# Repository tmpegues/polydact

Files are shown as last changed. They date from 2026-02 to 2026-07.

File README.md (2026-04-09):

# Polydact: a flexible extra digit
[Polydact on portfolio](tmpegues.github.io/project/polydact)
## Overview
Polydact is a wearable robotic sixth finger that gives its user greater dexterity than they have with their natural hand. The device is controlled by a glove with embedded flex sensors, as shown in the video below.

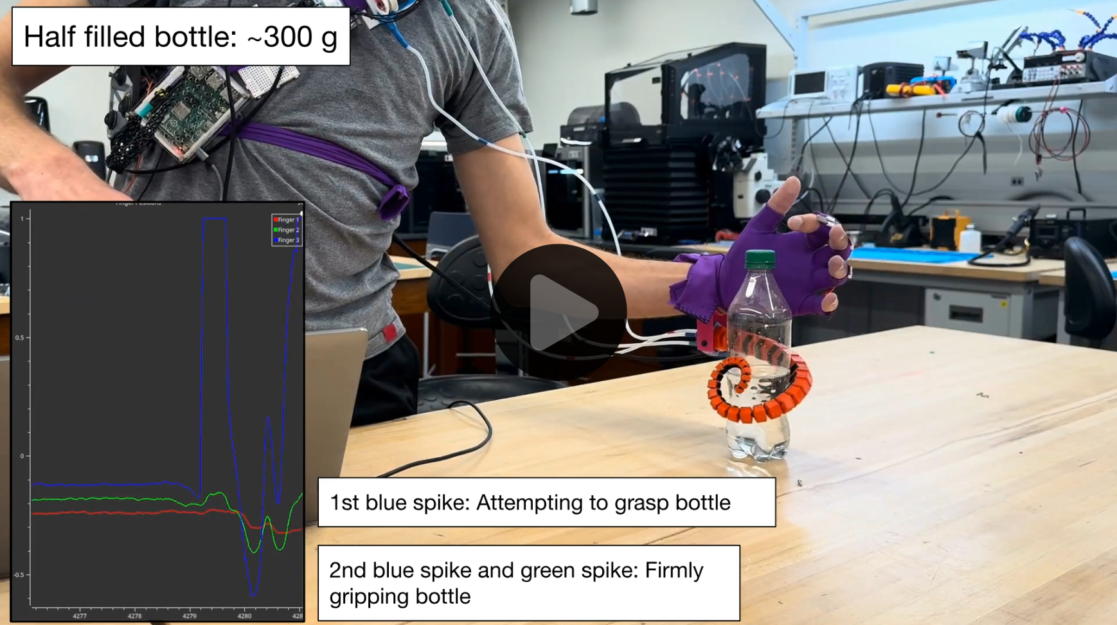
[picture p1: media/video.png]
Polydact in use (https://youtu.be/Mq05AG6Wxf4)

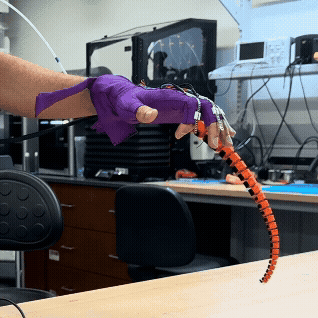
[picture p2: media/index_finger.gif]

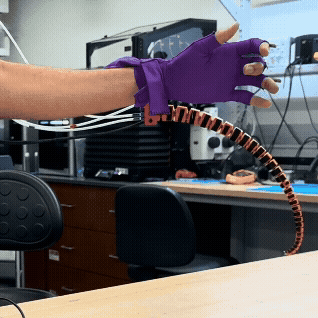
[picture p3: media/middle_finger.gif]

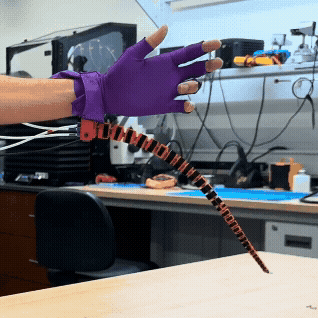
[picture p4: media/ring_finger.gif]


## Hardware Required
There are four main parts of the device: the tentacle itself, a control device, actuators, and electronics. *Italicized* parts are off the shelf parts that can be purchased. **Bolded** parts are custom designed and must be fabricated.

### 1. Tentacle
Four parts are required:
1. [**Tentacle**](/design/3d_files/multi_material_tentacle/)
    * Import all STL files to slicer as a single object with multiple parts
2. [**Socket**](/design/3d_files/hand_bracket/adjustable_mount_socket.stl)
3. [**Wrist mount**](/design/3d_files/hand_bracket/adjustable_mount_hand_bracket.stl)
4. A strap is also required to attach the wrist mount to the user.

### 2. Control Device
A glove with three flex sensors attached is the recommended control device. Below is an image and circuit diagram of the glove created for this project. It uses 3 *[Spectra Symbol flex sensors](https://www.adafruit.com/product/1070)*.

Control glove and circuit diagram

### 3. Actuation
Six parts are required:
1. *Motors*
    * *Robotis Dynamixel XM430-W210-T* were used for this project.
2. [**3x Motor Frames**](/design/3d_files/motor_parts/motor_frame.stl)
3. [**Motor Strap**](/design/3d_files/motor_parts/motor_strap/)
    * Import all STL files to slicer as a single object with multiple parts
4. [**3x Spools**](/design/3d_files/motor_parts/spool.stl)
    * [**Spool Tops**](/design/3d_files/motor_parts/spool_top.stl) are optional, but help retain tendons on spools
5. *A flexiblie, inextensible wire or thread to be used as a cable or tendon.* Braided fishing line is used for this project.
6. *Guide tubes* for routing the tendon from the motors to the tentacle.

### 4. Electronics
Two functions are required: the ability to interface with the control device and to interface with the motors. Two options are suggested:
1. Use a *Raspberry Pi* with external analog to digital converter (ADC). An eight-channel *MCP3008 ADC* is used for this project, but only three channels are required.
    * The Raspberry Pi will interface with the control device using the ADC and control the motors by connecting to the U2D2 using USB.
2. Use a laptop or other full featured computer connected by USB serial to a microcontroller with built-in ADC that interfaces with the control device.
    * [Example code](/pico_serial_sensor/) is provided to use a *Raspberry Pi Pico 2* to inferface with the control device.

Power: A 12 V battery can be used connected to the U2D2 Power Hub directly, and the Raspberry Pi through a buck converter to allow use of the device not tethered to an external power supply.

## Assembly
Using a battery powered Raspberry Pi for motor control with ADC for control device interface:
1. Thread tendons through the holes in the tentacle, socket, and guide tubes. Tie all three tendons in a knot at the free end of the tentacle.
    * It can be helpful to place two sections of heat-shrink tubing over on each guide tube to fix them to the socket and motor frames.
2. Place two M3 screw through holes on opposite faces of the socket and wrist mount. Adjust the angle of the socket relative to the wrist mount and tighten using nuts on the outside of the wrist mount.
3. If the tentacle is loose in the socket, hex nuts can be placed in the counterbores on the inside of the socket and screws can then be used to hold the tentacle in place.
4. Individually tie or otherwise fix the free ends of the the tendons to their own spools.
5. Screw spools onto motors and attach frames
    * If using heat shrink on guide tubes, this is a good time to shrink the tubes onto both the socket and motor frames
6. Attach switch box, Raspberry Pi, U2D2 and Power Hub, and motor strap to chest strap and tie diagonally across the user's chest.
7. Attach wrist mount to strap and tie strap to user's wrist.
8. Slide motors into motor strap.
9. Admire your handiwork

## ROS Setup
Packages `polydact` and `polydact_interfaces` are written for ROS 2 Kilted and can be downloaded and built with
```
git clone https://github.com/tmpegues/polydact.git
cd polydact
rosdep install --from-paths src --ignore-src
colcon build --paths src/*
source install/setup.bash
```
After installing dependencies, building workspace, and sourcing, you will be ready to launch.

## Launching
The main launchfile can be used with
```
ros2 launch polydact polydact.launch.xml sensor_source:=pi motors:=true control_mode:=0 plotter:=false
```
This will launch both the `pi_adc_sensor_node` and `motor_coordinator` nodes.
* `sensor_source` can be changed to `serial` to use a serial device over USB instead.
* `motors:=true` launches the `motor_coordinator` node.
    * If developing or troubleshooting a control device, `motors:=false` will not launch the `motor_coordinator_node`, allowing for focus on teh sensor node.
* `control_mode:=0` will initialize the motors with torque off.
    * After sensor calibration, motor torque can be activated with `ros2 service call /set_mode polydact_interfaces/srv/Mode '{mode: 1}'`
* `plotter:=false` will not open the PlotJuggler visualization of sensor positions.
    * When controlling the device from a Raspberry Pi, it is recommended to run PlotJuggler on another device that can receive the ROS topics so the Polydact user can see that their finger movements are being read properly.

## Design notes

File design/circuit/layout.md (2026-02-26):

Parts

| Part ID | Part | Location | Communication with | Power to | Power from |
| --- | --- | --- | --- | --- | --- |
| 01 | Battery | Belt | | 02, 03 | |
| 02 | Converter | Bandoleer | | 05 | 01 |
| 03 | U2D2 | Bandoleer | 04, 05 | | 01 |
| 04 | Motors | Shoulder strap | 03 | | |
| 05 | R Pi | Bandoleer | 03, 06, 08, 09, 10, 11 | 06, 08 | |
| 06 | ADC in (bread)board  | Bandoleer | 05, 07 | 07 | 05 |
| 07 | Flex Sensors | Glove | 06 | | 06 |
| 08 | Slide Pot | Bandolier | 05 | | 08 |
| 09 | Button 1 (Unlock) | Glove | 05 | | 05 |
| 10 | Button 2 (Loosen) | Glove | 05 | | 05 |
| 11 | Button 3 (Calibrate) | Bandolier | 05 | | 05 |
Wires

| IDs | Type | Length | Connectors |
| ----- | --- | --- | --- |
| 01_02 | Power | Short | |
| 01_03 | Power | Long | |
| 02_05 | Power | Long | X, USB-C |
| 03_04 | TTL | Short (available) | TTL |
| 05_03 | USB | Short (available) | USB-A, micro USB |
| 05_06 | Comm | Short | pin (3), pin (3) |
| 05_06 | Power | Short | pin (2), pin (4) |
| 05_08 | Comm and Power | Short | pin (4), pin (4) |
| 05_09 | Comm and Power | Long | pin (3), pin (2) |
| 05_10 | Comm and Power | Long | pin (3), pin (2) |
| 05_11 | Comm and Power | Short | pin (2), pin (2) |

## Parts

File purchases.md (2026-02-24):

| Category | Item | PN | Qty | Total Price | Put on sheet? | Received |
| --- | --- | --- | --- | --- | --- | --- |
| Glove | [Batting gloves](https://www.amazon.com/Franklin-Sports-20965F4-Shok-Sorb-Batting/dp/B07GJQBRMX) | | 2 Pair | 34.52 | 0113 | O |
| Glove | [Flex Sensors](https://www.adafruit.com/product/1070#technical-details) | | 10 | 71.60 | 0113 | O |
| Glove | [Stretch Rubber Sensor](https://www.adafruit.com/product/519) | | X | - | Lab Stock | O |
| Tentacle | [KV Flex 90](https://www.reynoldsam.com/product/kxflex) | | 1 | 34.47 | 0129 | O |
| Glove | [Conductive Nylon Tape](https://www.adafruit.com/product/3961) | | 1 | 2.95 | 0205 | O |
| Glove | [Velostat Sheet](https://www.adafruit.com/product/1361) | | 1 | 4.95 | 0205 | O |
| Glove | [Sewing Snaps](https://www.adafruit.com/product/1126) | | 1 | 3.95 | 0205 | O |
| Glove | [Steel Thread](https://www.adafruit.com/product/640) | | 1 | 6.95 | 0205 | O |
| Glove | [Lycra](https://www.amazon.com/Spandex-Fabric-Swimwear-Activewear-Stretch/dp/B0CJHF49Y2) | | 2 yd | 31.80 | 0205 | O |
| Glove | [Stretch iron-on tape](https://www.amazon.com/HeatnBond-SoftStretch-Ultra-Iron-Adhesive/dp/B01N1T2IYZ) | | 1 | 4.43 | 0205 | O |
| Glove | [Neoprene](https://www.amazon.com/FLKQC-Neoprene-Adhesive-Multiple-Dimensions/dp/B09TXFBNWH) | | 1 | 10.99 | 0205 | O |
| Mechanical  | [PTFE Tubing 4 OD, 2 ID](https://www.mcmaster.com/52335K32/) | | 10 ft  | 31.20 | x | O |
| Mechanical  | [PE Tubing, 4 OD](https://www.mcmaster.com/51555K121/) | | 25 ft  | 8.25 | 0220 | O |
| Electronics | [Rasberry Pi 4, 4 GB](https://www.adafruit.com/product/4296) | Ada 4296 | 1 | 75.00 | 0224 | X |
| Electronics | [MCP3008 ADC](https://www.adafruit.com/product/856) | 856 | 1 | 4.50 | 0224 | X |
| Electronics | [UEBC Buck Converter](https://www.adafruit.com/product/1385) | | 1 | 9.95 | 0224 | X |
| Electronics | [NeoSlider](https://www.adafruit.com/product/5295) | | 1 | x | Lab Stock | O |
| x | x | | x | x | x | x |
| x | x | | x | x | x | x |

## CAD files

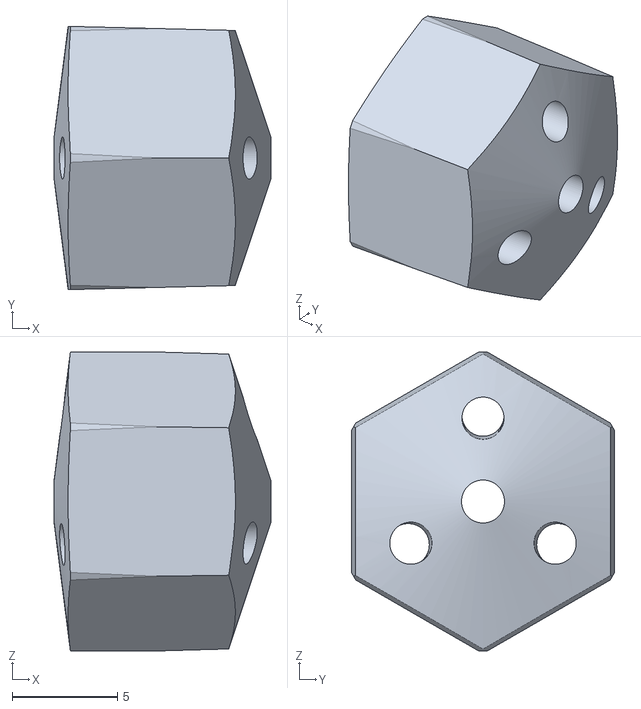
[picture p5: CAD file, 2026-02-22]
design/3d_files/multi_material_tentacle/3D for full printing - Part 13.stl
10.3 x 12.5 x 14.2

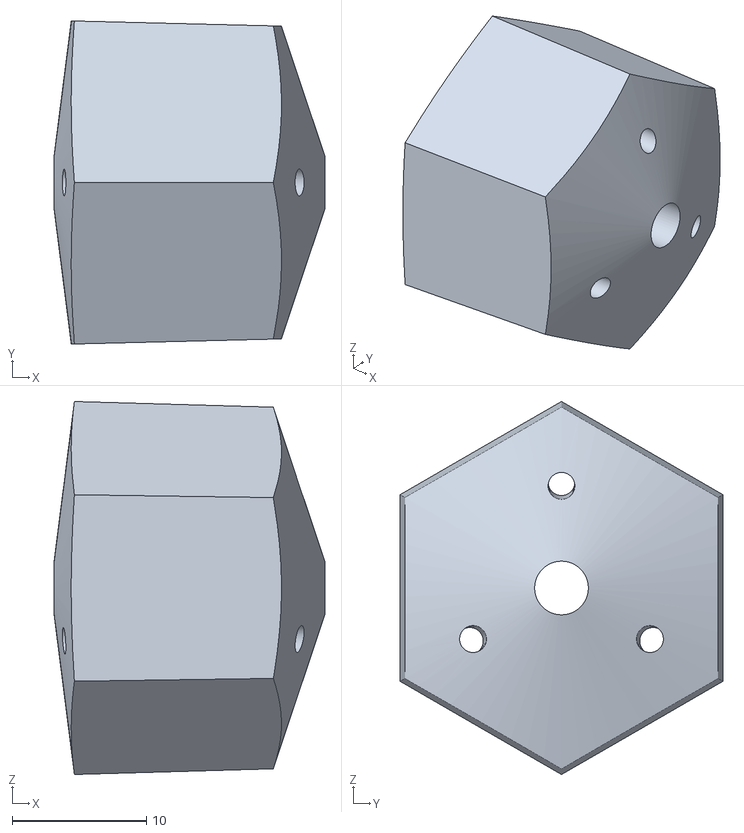
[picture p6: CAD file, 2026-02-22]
design/3d_files/multi_material_tentacle/3D for full printing - Part 28.stl
20.2 x 24.1 x 27.8

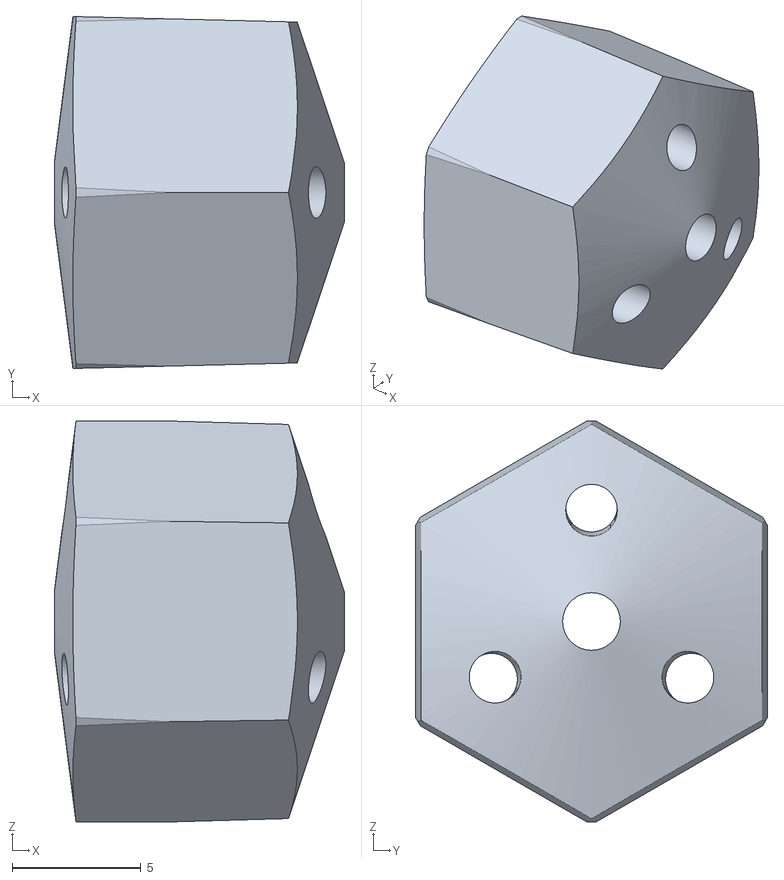
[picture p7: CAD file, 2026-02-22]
design/3d_files/multi_material_tentacle/3D for full printing - Part 15.stl
11.3 x 13.6 x 15.5

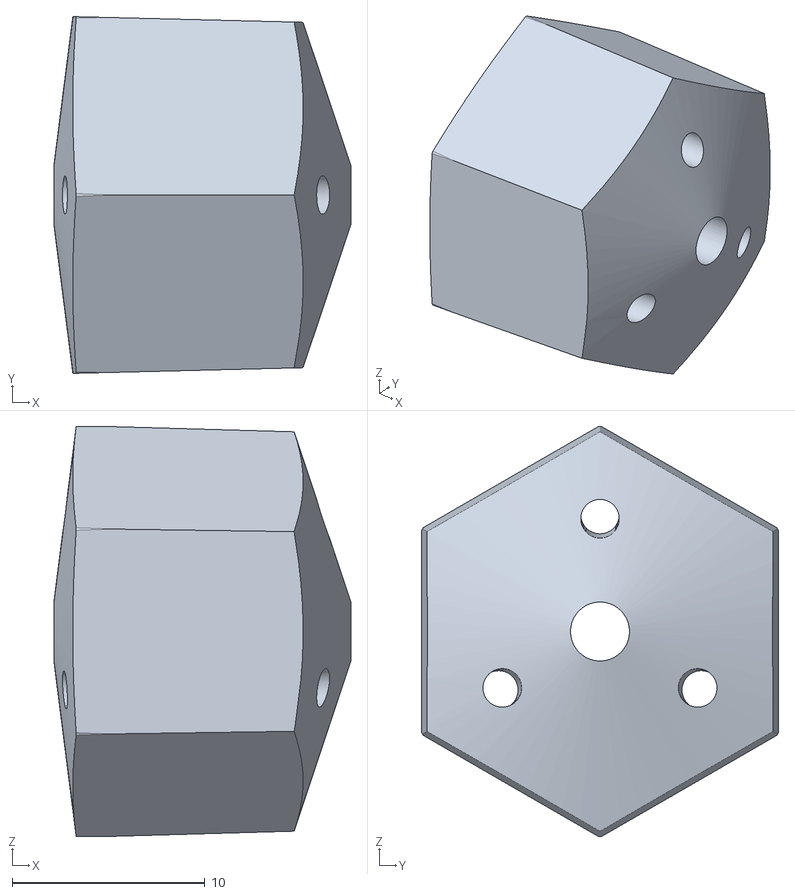
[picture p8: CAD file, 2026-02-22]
design/3d_files/multi_material_tentacle/3D for full printing - Part 22.stl
15.4 x 18.5 x 21.3

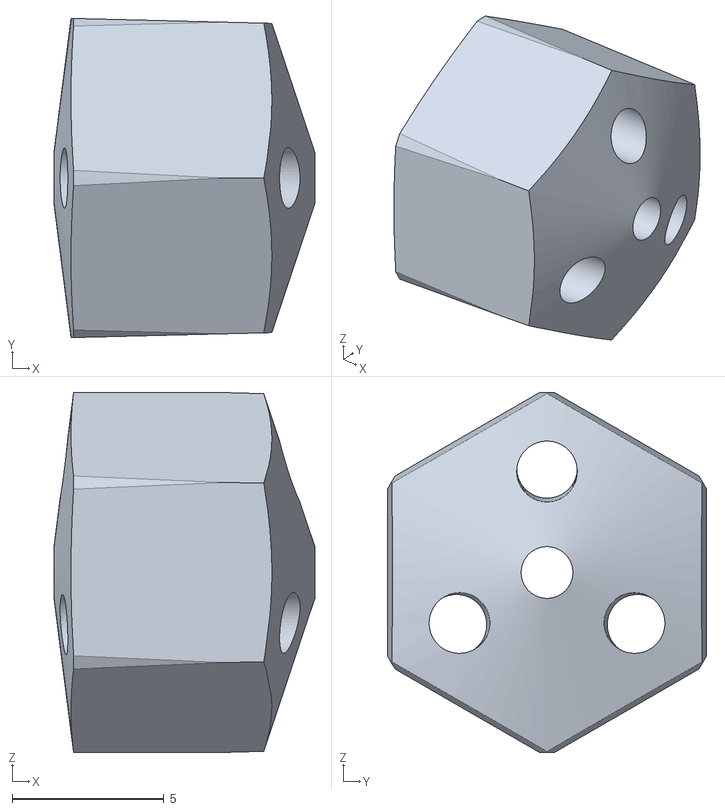
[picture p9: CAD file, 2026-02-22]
design/3d_files/multi_material_tentacle/3D for full printing - Part 9.stl
8.60 x 10.5 x 11.9

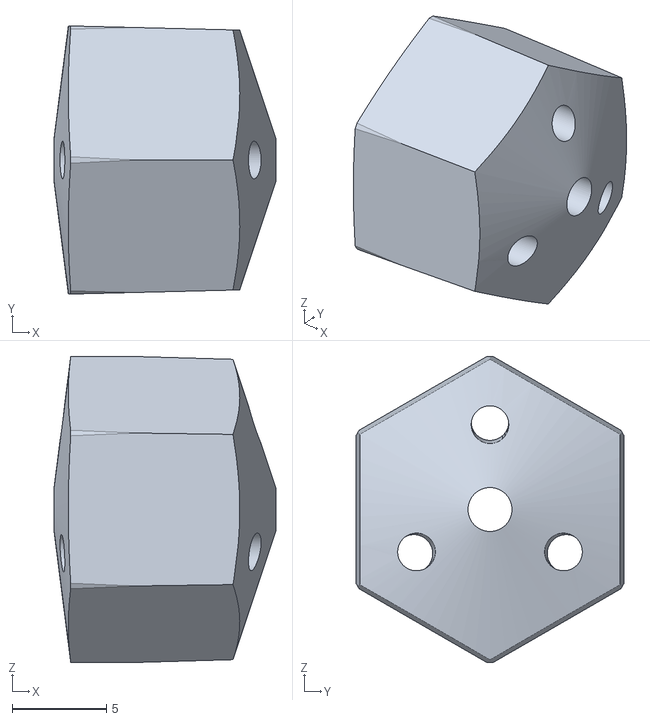
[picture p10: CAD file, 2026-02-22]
design/3d_files/multi_material_tentacle/3D for full printing - Part 16.stl
11.8 x 14.3 x 16.3

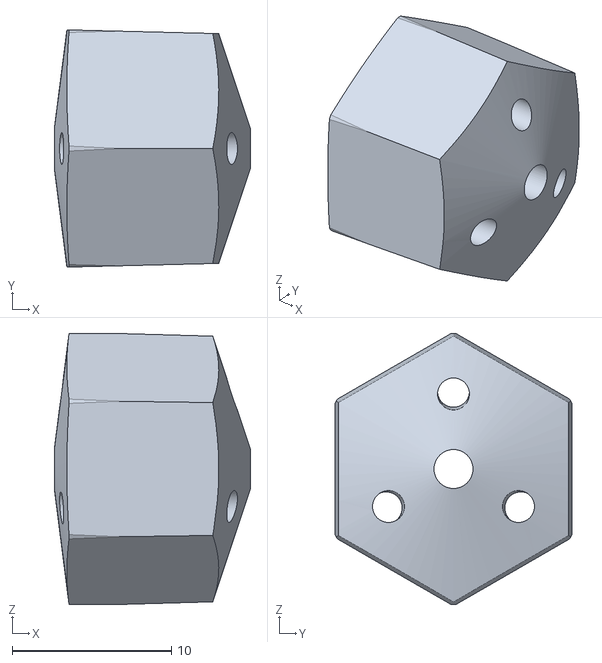
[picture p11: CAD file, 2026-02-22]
design/3d_files/multi_material_tentacle/3D for full printing - Part 17.stl
12.3 x 14.9 x 17.0

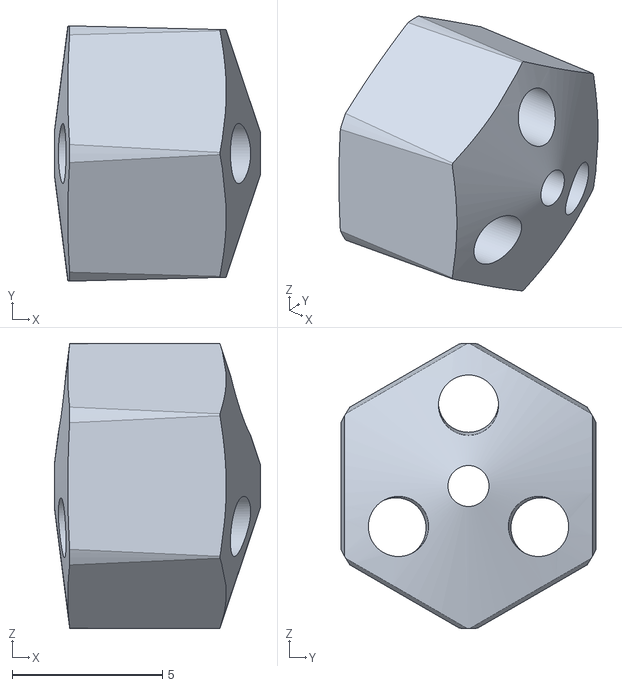
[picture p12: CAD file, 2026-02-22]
design/3d_files/multi_material_tentacle/3D for full printing - Part 4.stl
6.87 x 8.50 x 9.49

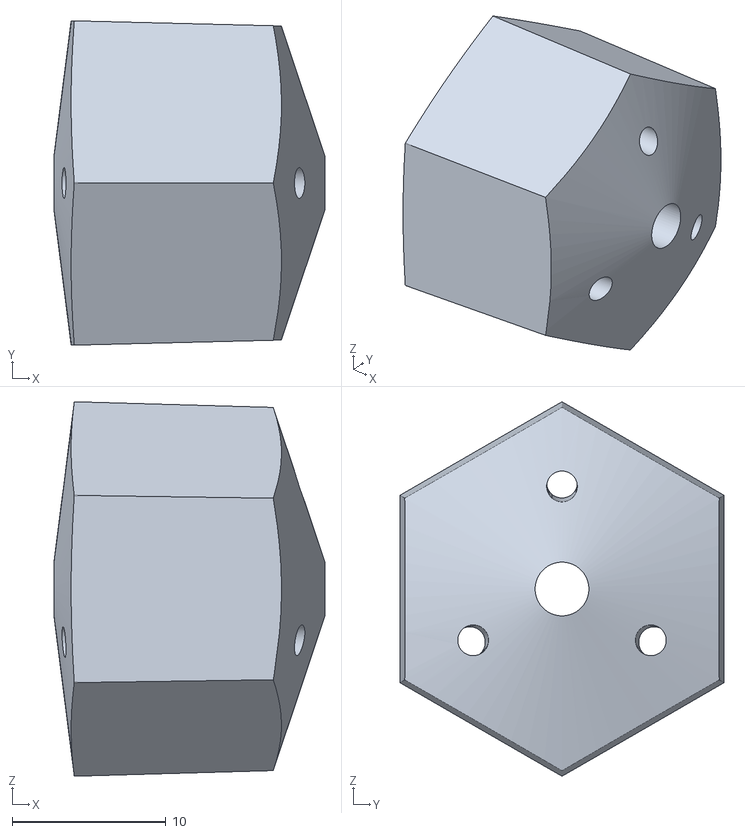
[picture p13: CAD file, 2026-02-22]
design/3d_files/multi_material_tentacle/3D for full printing - Part 25.stl
17.6 x 21.1 x 24.4

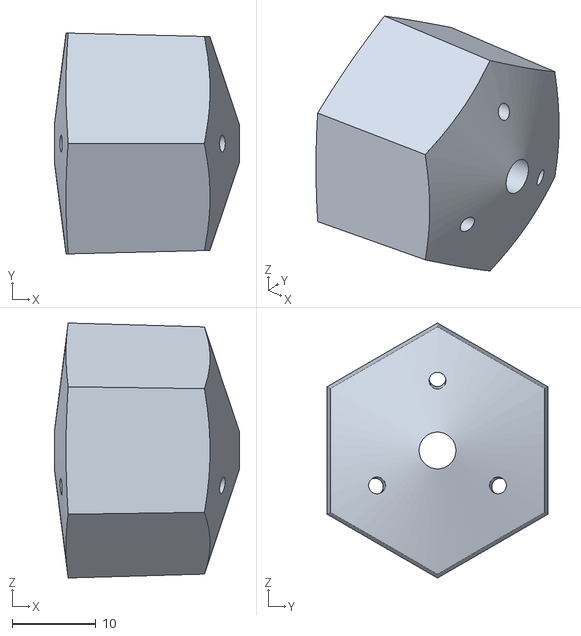
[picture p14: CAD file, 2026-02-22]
design/3d_files/multi_material_tentacle/3D for full printing - Part 30.stl
22.1 x 26.3 x 30.4

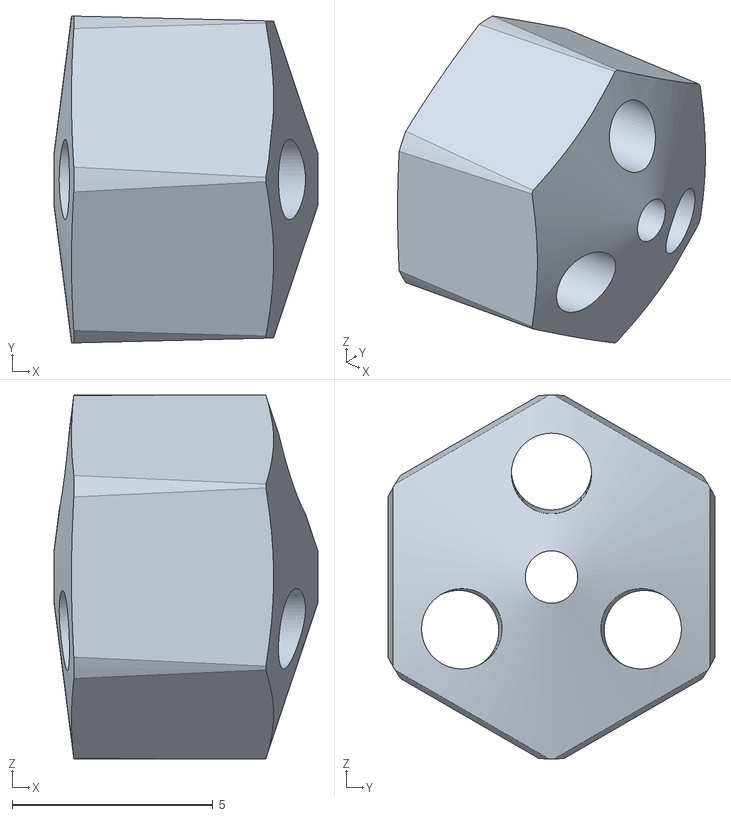
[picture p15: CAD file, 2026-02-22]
design/3d_files/multi_material_tentacle/3D for full printing - Part 3.stl
6.57 x 8.15 x 9.07

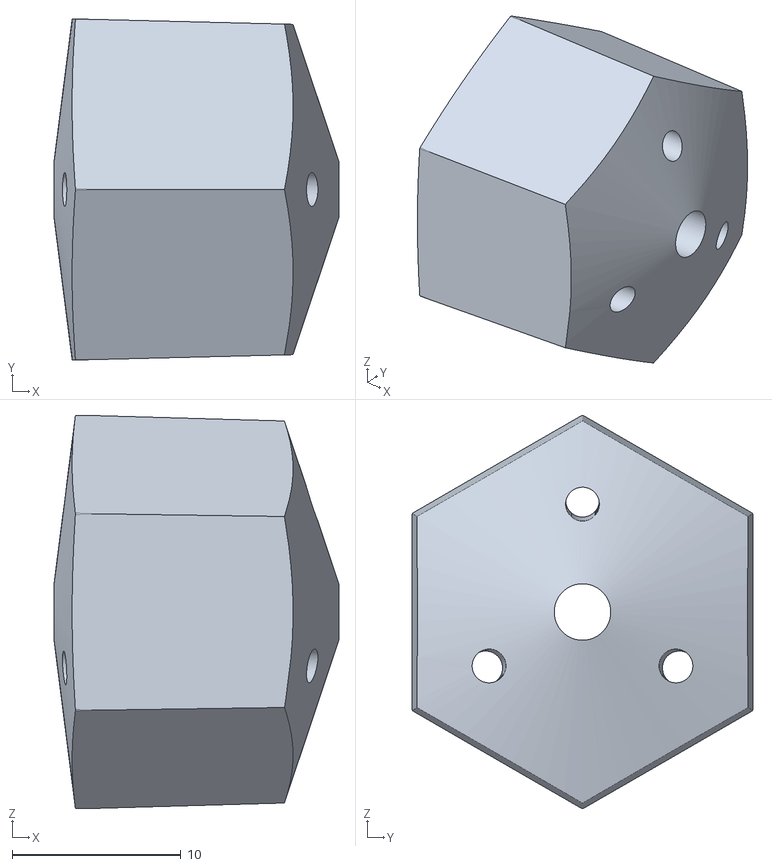
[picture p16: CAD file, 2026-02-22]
design/3d_files/multi_material_tentacle/3D for full printing - Part 24.stl
16.9 x 20.2 x 23.3

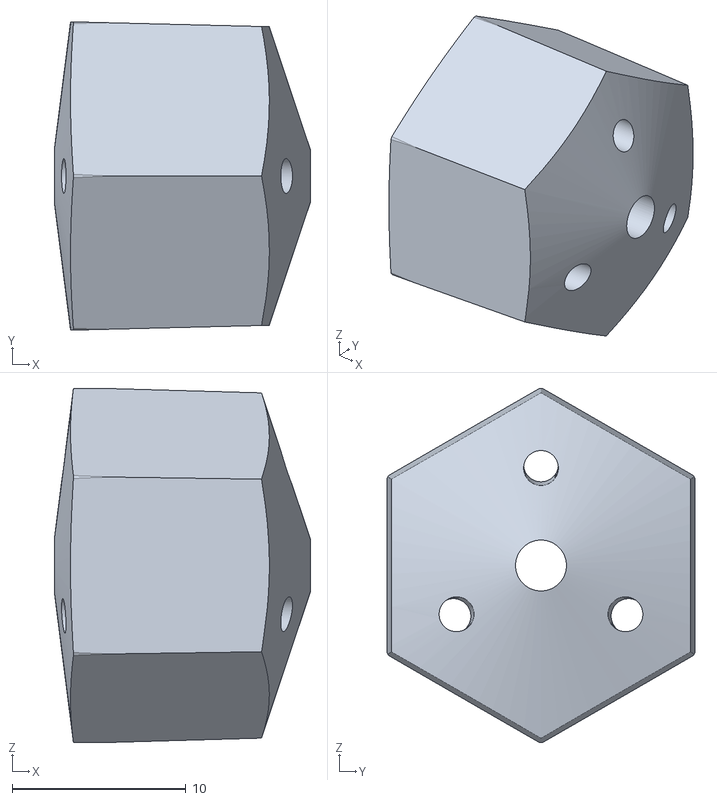
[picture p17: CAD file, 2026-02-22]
design/3d_files/multi_material_tentacle/3D for full printing - Part 21.stl
14.7 x 17.7 x 20.4

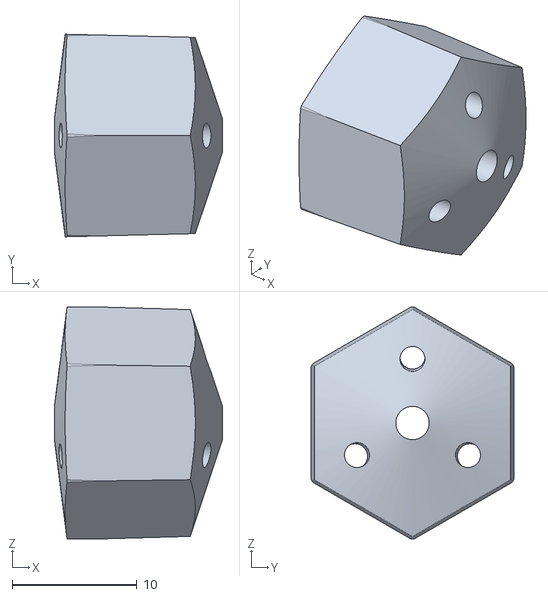
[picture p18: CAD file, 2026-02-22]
design/3d_files/multi_material_tentacle/3D for full printing - Part 19.stl
13.5 x 16.2 x 18.6

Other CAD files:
design/3d_files/multi_material_tentacle/3D for full printing - Part 11.stl
design/3d_files/multi_material_tentacle/3D for full printing - Part 29.stl
design/3d_files/multi_material_tentacle/3D for full printing - Part 12.stl
design/3d_files/multi_material_tentacle/3D for full printing - Part 20.stl
design/3d_files/flex_slider.stl
design/3d_files/hand_bracket/adjustable_mount_hand_bracket.stl
design/3d_files/hand_bracket/adjustable_mount_socket.stl
design/3d_files/motor_parts/motor_base.stl
design/3d_files/motor_parts/motor_frame.stl
design/3d_files/motor_parts/motor_strap/strap_band.stl
design/3d_files/motor_parts/motor_strap/strap_slide_base_single (1).stl
design/3d_files/motor_parts/motor_strap/strap_slide_base_single (2).stl
design/3d_files/motor_parts/motor_strap/strap_slide_base_single.stl
design/3d_files/motor_parts/spool.stl
design/3d_files/motor_parts/spool_top.stl
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

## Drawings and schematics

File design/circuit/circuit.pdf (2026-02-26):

05

06

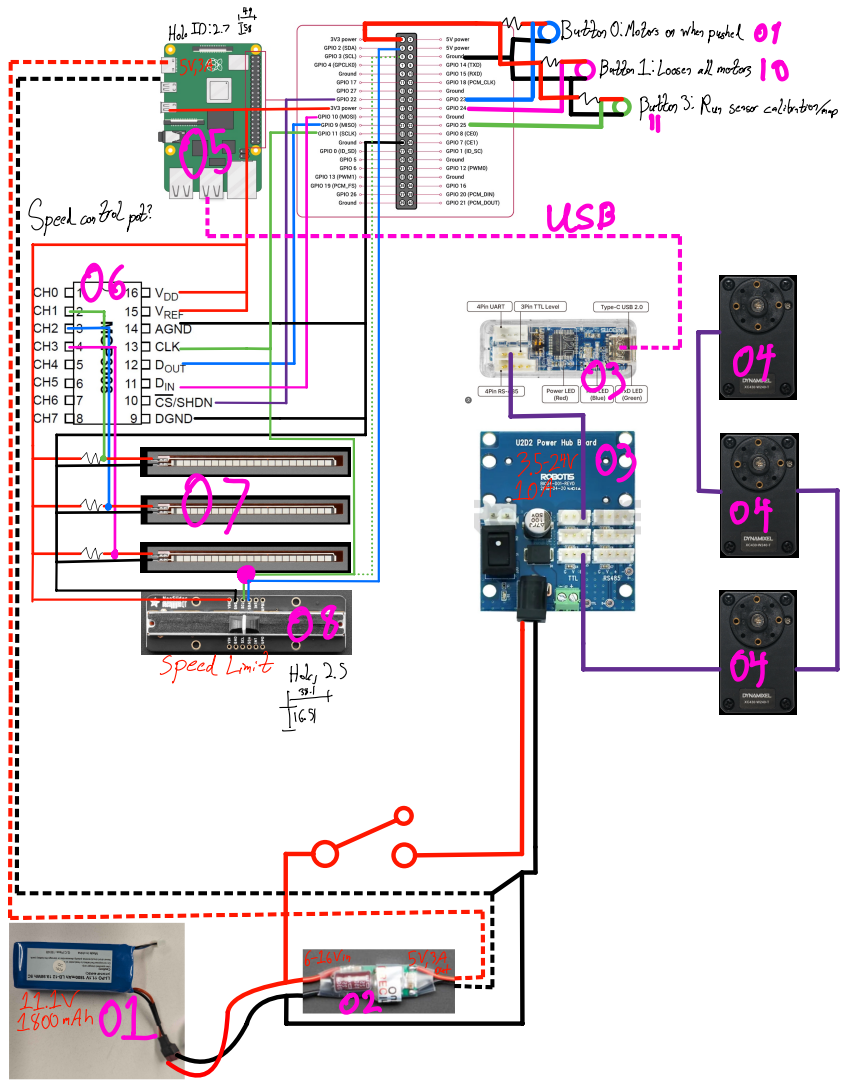
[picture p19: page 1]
Hol.IO27 I; ButtonOMotorsonwhenpushed09; Button1Loose allmotors 0; Python Runsensorcalibrationmap; Speedcontrolpot; USB; 08 04 speedlinitI.fi; 6 16Vin5V 3Aut-1EtAnO1 ⁰²

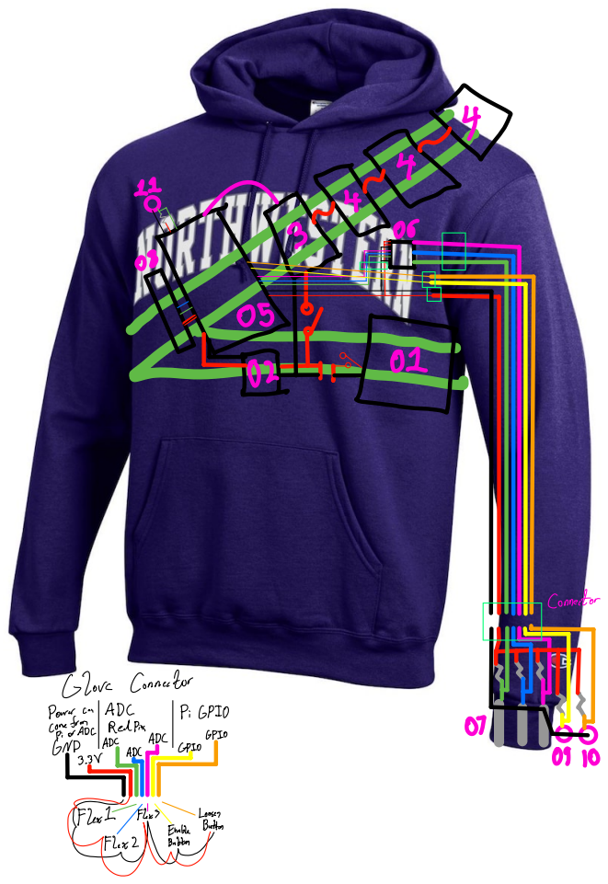
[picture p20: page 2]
Connector; 222 Glove Connector; t.itiianii; Ellenville

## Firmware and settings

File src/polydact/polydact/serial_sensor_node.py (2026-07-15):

"""Read the serial monitor from the Pico 2 to publish a motor goal."""

from polydact_interfaces.msg import MotorGoal
import rclpy
from rclpy.node import Node
from rclpy.qos import QoSDurabilityPolicy, QoSProfile
from std_srvs.srv import Empty
from polydact.sensor import Sensor

import serial


class SerialReader(Node):
    """Reads the serial monitor and publishes motor goals."""

    def __init__(self):
        """Initialize serial reader and goal publisher."""
        super().__init__('serial_reader')

        # Creating publisher first to that PlotJuggler doesn't have to wait for calibration
        self.goal_pub = self.create_publisher(
            MotorGoal,
            'motor_goal',
            QoSProfile(depth=10, durability=QoSDurabilityPolicy.TRANSIENT_LOCAL),
        )

        self.remap_srv = self.create_service(Empty, 'remap', self.remap_cb)

        # Get motor list and initialize sensors
        self.declare_parameter('sensor_ids', [1, 2, 3])
        sensor_ids = self.get_parameter('sensor_ids').value

        self.declare_parameter('motor_ids', [1, 2, 3])
        self.motor_ids = self.get_parameter('motor_ids').value

        self.declare_parameter('calibration_len', 400)
        self.calibration_len = self.get_parameter('calibration_len').value

        self.sensors = {}
        for sensor_id, motor_id in zip(sensor_ids, self.motor_ids):
            self.sensors.update({sensor_id: Sensor(sensor_id, motor_id)})

        # Set up serial port
        self.declare_parameter('serial_port', '/dev/ttyACM0')
        port = self.get_parameter('serial_port').value
        self.get_logger().info(f'serial port: {port}')

        self.s_port = False
        while not self.s_port:
            try:
                self.s_port = serial.Serial(port, 115200, timeout=10)
            except serial.SerialException:
                self.get_logger().error('Serial device not found.', throttle_duration_sec=1)

        # Calibrate sensor min/max with specified number of readings from each sensor
        self.min_max_calibration(self.calibration_len)

        # Begin publishing normalized sensor readings
        self.pub_freq = 100
        read_freq = 300
        self.last_published = 0
        # Make sure I'm reading slightly faster than serial is printing
        read_freq *= len(self.sensors) + 0.1

        self.reading_timer = self.create_timer(1 / read_freq, self.reading_timer_callback)
        self.publishing_timer = self.create_timer(
            1 / self.pub_freq, self.publishing_timer_callback
        )
        self.get_logger().info('Serial Reader fully initialized')

    def full_calibration(self, num_points: int):
        """
        Calibrate the glove by finding min and max flexes for all fingers, then remap to motors.

        Args:
        ----
        num_points (int): How many points are to be collected for the min max calibration?

        """
        self.freeze(True)

        self.min_max_calibration(num_points)
        self.map_sensor_to_motor()

        self.freeze(False)

    def freeze(self, freeze_on: bool, read: bool = False):
        """
        Stop all motors by pausing timer, then sending Goal = 0.

        Saving of sensor values can also be paused optionally, but unfreezing will always restart
        sensor saving.

        Args:
        ----
        freeze_on (bool): True will stop motors, False will turn velocity control back on
        read (bool): True will also top lines from being saved, which is used for remapping.

        """
        match freeze_on:
            case True:
                if read:
                    self.reading_timer.cancel()
                self.publishing_timer.cancel()
                for motor_id in self.motor_ids:
                    self.goal_pub.publish(MotorGoal(motor_id=motor_id, goal=0))

            case False:
                for sensor in self.sensors.values():
                    sensor.fill_average()
                self.publishing_timer.reset()
                self.reading_timer.reset()

    def get_max_diff(self, reads: int = 100) -> int:
        """
        Get the ID of the sensor that gets bent the most over the next selected no of serial lines.

        Args:
        ----
        reads (int): How many serial lines to read. Not how many per sensor.

        Returns
        -------
         (int): The ID of the sensor that experienced the largest bend. -1 means there was an issue

        """
        # Clear the saved selector values
        for sensor in self.sensors.values():
            sensor.selector_min = 10000
            sensor.selector_max = -10000

        i = 0
        # Read the selected total number of lines
        while i <= reads:
            line = self.get_line()
            if line:
                id, read = line
                if id not in self.sensors:
                    self.get_logger().error(f'Sensor message id {id} is not valid id.')
                    break
                sensor = self.sensors[id]
                if read > sensor.selector_max:
                    sensor.selector_max = read
                elif read < sensor.selector_min:
                    sensor.selector_min = read
                else:
                    self.get_logger().error(
                        f'Unexpected condition in sensor remapping. Serial line: {line}'
                    )

        # Now that lines are read, determine which sensor has been flexed the most
        diff = 0
        max_bent = -1
        for id, sensor in self.sensors.items():
            if abs(sensor.selector_max - sensor.selector_min) > diff:
                diff = sensor.selector_max - sensor.selector_min
                max_bent = id

        return max_bent

    def remap_cb(self, request, response):
        """
        Remap sensors.

        Args:
        ----
        request (std_srv/srv/Empty): unused
        response (std_srv/srv/Empty): unused

        """
        self.map_sensor_to_motor()

    def map_sensor_to_motor(self):
        """Change the assignment of which sensor controls which motor."""
        self.freeze(True, True)
        retry = True
        while retry:
            retry = False
            # Clear motor ids for all sensors
            for sensor in self.sensors.values():
                sensor.motor_id = -1

            # Cycle through motors again, setting sensors as we go
            for motor in self.motor_ids:
                self.get_logger().info(f'Motor: {motor}')
                while True:
                    self.get_logger().info(f'Wiggle the sensor to use with motor {motor}')
                    # Read for 100 values, find max bent sensor
                    sensor1 = self.get_max_diff(100)
                    self.get_logger().info(f'Sensor {sensor1} selected for {motor}')
                    self.get_logger().info(f'Keep wiggling sensor {sensor1} to confirm selection')
                    # Read another 100, check for match
                    sensor2 = self.get_max_diff(100)
                    # If the sensors match and that sensor doesn't have a motor saved yet, save
                    if sensor1 == sensor2 and self.sensors[sensor1].motor_id == -1:
                        self.sensors[sensor1].motor_id = motor
                        self.get_logger().info(f'Saving: Sensor {sensor1} maps to motor {motor}')
                        break
                    elif sensor1 != sensor2:
                        self.get_logger().error(
                            f'1st sensor {sensor1} and 2nd sensor {sensor2} do not match.'
                        )
                    elif self.sensors[sensor1].motor_id != -1:
                        self.get_logger().error(
                            f'Sensor {sensor1} already assigned: {self.sensors[sensor1].motor_id}.'
                        )
                    self.get_logger().info(f'Retrying. Motor = {motor}.')

            # Check that each sensor has a motor (id != -1) and that each motor is unique
            motor_list = self.motor_ids.copy()
            for s_id, sensor in self.sensors.items():
                if sensor.motor_id in motor_list:  # This case is what we want
                    self.get_logger().info(f'Sensor {s_id} is assigned to motor {sensor.motor_id}')
                    motor_list.remove(sensor.motor_id)
                elif sensor.motor_id == -1:
                    retry = True
                    self.get_logger().error(f'Sensor {s_id} was not assigned a motor')
                    break
                elif sensor.motor_id not in motor_list:
                    retry = True
                    self.get_logger().error('This motor is already  assigned or is invalid ID.')
                    break
                else:
                    self.get_logger().error(f'Unexpected case. S: {s_id}, M: {sensor.motor_id}')

            # Check that each motor was assigned
            if len(motor_list) != 0:
                retry = True
                self.get_logger().error(f'Motors unassigned: {motor_list}.')

            if retry:
                self.get_logger().info('Retrying remapping.')
            else:
                self.get_logger().info('Remapping complete:')
                for sensor in self.sensors.values():
                    self.get_logger().info(f'Sensor {sensor.sensor_id} -> Motor {sensor.motor_id}')
                self.freeze(False)

    def min_max_calibration(self, num_points: int):
        """
        Read values from the connected sensors for a few seconds to determine ranges.

        Args:
        ----
        num_points (int): How many points will be checked to figure out each sensor's min/max range

        """
        calibrated = 0
        loop = 0
        self.get_logger().info(f'Beginning min/max calibration for {len(self.sensors)} sensors.')
        while calibrated < len(self.sensors) * num_points:
            self.get_logger().info(
                f'Loop {loop} ({calibrated}/{len(self.sensors) * num_points})',
                throttle_duration_sec=1,
            )
            loop += 1
            line = self.get_line()
            if line:
                id, read = line
                if id not in self.sensors:
                    self.get_logger().error(f'Sensor message id {id} is not valid id.')
                    break
                sensor = self.sensors[id]
                if sensor.calibrated >= num_points:
                    # If we've already read many points, do not process any further points
                    pass
                elif sensor.calibrated < num_points:
                    # If we haven't read this many points, check against min and max
                    sensor.calibrated += 1
                    calibrated += 1
                    if read > sensor.max:
                        sensor.max = read
                    elif read < sensor.min:
                        sensor.min = read
                    if sensor.calibrated >= num_points:
                        self.get_logger().info(
                            f'Sensor {sensor.sensor_id} has all {num_points} min/max points read.'
                        )
                        sensor.fill_average()
                else:
                    self.get_logger().error(
                        f'Unexpected condition in calibration. Serial line: {line}'
                    )
        self.get_logger().info('Sensor min/max calibration complete:')
        for id, sensor in self.sensors.items():
            self.get_logger().info(f'Sensor {sensor.sensor_id}: {sensor.min} - {sensor.max}')

    def get_line(self):
        """
        Get the most recent serial line.

        Returns
        -------
        (Bool or (int, float)): False if no or invalid serial read, (id, read) if the was valid

        """
        result = False
        line = False
        try:
            line = self.s_port.readline().decode('utf-8').strip()
        except serial.SerialException:
            self.get_logger().error('No device.')
        if line:
            id = int(line[0])
            if id in self.sensors:
                try:
                    read = float(line[2:])
                    result = (id, read)
                    self.get_logger().debug(f'Read: {line}')
                except ValueError:
                    self.get_logger().error(f'Faulty serial line: {line}')

            else:
                self.get_logger().error(f'Unexpected serial line: {line}')
        else:
            self.get_logger().debug('No serial line available.')
        return result

    def reading_timer_callback(self):
        """Read the serial monitor."""
        line = self.get_line()
        if line and line[0] in self.sensors.keys():
            self.sensors[line[0]].new_read(line[1])

    def publishing_timer_callback(self):
        """Publish all motor goals individually."""
        self.get_logger().debug('Publishing Timer')

        self.goal_pub.publish(
            MotorGoal(
                motor_id=self.sensors[list(self.sensors.keys())[self.last_published]].motor_id,
                goal=self.sensors[list(self.sensors.keys())[self.last_published]].get_value(),
            )
        )
        self.last_published += 1
        self.last_published %= len(self.sensors)


def main(args=None):
    """Run the serial_reader node."""
    rclpy.init(args=args)
    node = SerialReader()
    rclpy.spin(node)
    rclpy.shutdown()


if __name__ == '__main__':
    main()

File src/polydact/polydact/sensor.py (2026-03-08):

"""Reading Polydact's flex sensors."""


class Sensor:
    """Sensor class holds values for each individual sensor."""

    def __init__(self, sensor_id, motor_id):
        """
        Initialize the sensor.

        Args:
        ----
        sensor_id (int): Which sensor is this? My finger map is 1 = ring, 2 = middle, 3 = index.
        motor_id (int): What is the Dynamixel ID of the motor that this sensor will control?

        """
        self.sensor_id = sensor_id
        self.motor_id = motor_id
        self.min = 10000.0
        self.max = 0.0
        self.selector_min = 0.0
        self.selector_max = 0.0
        self.smoothing = 10
        self.reads = [0.0] * self.smoothing
        self.calibrated = 0

    def new_read(self, value: float):
        """
        Add the newest raw sensor reading to the rolling list.

        Args:
        ----
        value (float): The new reading to add to the rolling list.

        """
        self.reads.append(value)
        self.reads.pop(0)

    def get_value(self) -> float:
        """
        Get the normalized rolling average of sensor readings.

        Returns
        -------
         (float): The normalized rolling average of sensor readings. If sensor is uncalibrated,
                  0.0 will be returned (freezes the motors).

        """
        if not self.calibrated:
            return float(0.0)
        else:
            value = sum(self.reads) / self.smoothing  # Average
            value -= (self.max + self.min) / 2  # Center at 0
            value /= (self.max - self.min) / 2  # Squash the values down to -1 to 1

            # If the max and min are off for some reason, clamp the values
            if value > 1:
                value = 1
            elif value < -1:
                value = -1
            return float(value)

    def fill_average(self):
        """Fill the reads list with a neutral value so motors initialize stopped."""
        self.reads = [(self.max + self.min) / 2] * self.smoothing

    def reset(self):
        """Clear the calibrated values, but keep the motor id assignment."""
        self.min = 10000
        self.max = 0.0
        self.reads = [0.0] * self.smoothing
        self.calibrated = 0

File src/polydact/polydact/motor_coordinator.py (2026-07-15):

"""Test different control modes of one Dynamixel motor."""

from polydact.dynamixel_interface import Motor, DynamixelInterface
from polydact_interfaces.msg import MotorGoal

from polydact_interfaces.srv import Mode
import rclpy
from rclpy.node import Node
from rclpy.qos import QoSDurabilityPolicy, QoSProfile
from sensor_msgs.msg import JointState
from std_msgs.msg import Header


class MotorCoordinator(Node):
    """
    MotorCoordinator is the intermediary between the control device (glove) and the motors.

    Publishers:
        + "motor_states" (sensor_msgs/msg/JointState) - Actual states of the motors

    Subscribers:
        + "motor_goal" (polydact_interfaces/msg/MotorGoal) - A goal to set a particular motor to

    Services:
        + "set_mode" (polydact_interfaces/srv/Mode) - What Control Mode to set the motor to.
            (0 (off), 1 (vel))

    Parameters
    ----------
        + "motor_ids" - The motor ID to to control with this node
        + "control_mode" - The initial Control Mode to use

    """

    def __init__(self):
        """Initialize motor control."""
        super().__init__('motor_coordinator')
        self.active = 0

        self.dyn = DynamixelInterface(self)

        # Set motors to my settings
        self.declare_parameter('motor_ids', [1, 2, 3])
        self.motor_ids = self.get_parameter('motor_ids').value

        self.declare_parameter('Control_Mode', 1)
        self.mode = self.get_parameter('Control_Mode').value

        self.motors = {}
        for motor_id in self.motor_ids:
            self.motors.update({motor_id: Motor(self.dyn, motor_id)})

        # Motors should initialize off, but loop through just to be sure
        # Should probably ad a check to make sure they're actually all off
        for motor in self.motors.values():
            motor.set_off()

        self.goal_sub = self.create_subscription(
            MotorGoal,
            'motor_goal',
            self.set_single_goal,
            QoSProfile(depth=10, durability=QoSDurabilityPolicy.TRANSIENT_LOCAL),
        )
        self.mode_srv = self.create_service(Mode, 'set_mode', self.switch_mode_cb)

        self.motor_states_pub = self.create_publisher(JointState, 'motor_states', 10)

        self.posi_pub = self.create_publisher(MotorGoal, 'cur_position', 10)
        self.velo_pub = self.create_publisher(MotorGoal, 'cur_velocity', 10)
        self.load_pub = self.create_publisher(MotorGoal, 'cur_load', 10)

        # State reads are blocking serial round-trips; at 100 Hz they saturate the
        # bus and starve the command path. 20 Hz is plenty for telemetry.
        self.timer = self.create_timer(1 / 20, self.timer_callback)
        self.get_logger().info(f'motors: {self.motors.keys()}')
        for motor in self.motors.values():
            motor.set_mode(1)

        self.get_logger().info('Motor Coordinator ready')

    def set_single_goal(self, msg: MotorGoal):
        """
        Set the position, velocity, or PWM goal for a single motor.

        Args:
        ----
        msg (polydact_interfaces/msg/MotorGoal): msg.motor_id is the motor to set the goal for
                                                  msg.goal is the goal to set to

        """
        self.get_logger().debug(f'MotorGoal {msg.motor_id} {msg.goal} received.)')
        if msg.motor_id not in self.motors.keys():
            self.get_logger().error(f'Unexpected motor id received: {msg}')
            return

        deadzone = 0.3
        self.motors[msg.motor_id].set_velocity(-1 * msg.goal, deadzone)

    def switch_mode_cb(self, request, response):
        """
        Switch the control mode of this node's motor.

        Args:
        ----
        request  (polydact_interfaces/srv/Mode):
                request.mode contains value to set as the motor's control mode.
        response (polydact_interfaces/srv/Mode):
                reponse.success is True if the control mode is successfully changed

        """
        response.success = True

        # Filter out invalid values
        if request.mode not in [0, 1]:
            self.get_logger().error(
                f'{request.mode} not valid Control Mode. Use 0 (off), 1 (velocity)'
            )
            response.success = False

        for motor in self.motors.values():
            motor.set_mode(request.mode)

        return response

    def timer_callback(self):
        """Read and publish motor position, velocity, and load."""
        motor_states = JointState(header=Header(stamp=self.get_clock().now().to_msg()))

        for motor in self.motors.values():
            motor.get_state()
            # TODO: Add some sort of checking for if the get_state fails
            motor_states.name.append(str(motor.motor_id))
            motor_states.position.append(motor.position)
            motor_states.velocity.append(motor.velocity)
            motor_states.effort.append(motor.effort)

        self.motor_states_pub.publish(motor_states)


def main(args=None):
    """Run the node."""
    rclpy.init(args=args)
    node = MotorCoordinator()
    rclpy.spin(node)
    rclpy.shutdown()


if __name__ == '__main__':
    main()

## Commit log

2026-01-09 Adding reference. Added modified springs.
    [spring_8mm.stl, spring_8mm_no_mid.stl]
2026-01-12 Adding references and changing to tentacle digit
    Next steps:
    [3_cable_SpiRob.STL, pegues_bone_unit_v1.gcode.3mf]
2026-01-12 New flexible tentacle print parts.
    [3D - Part 1.stl, 3D - Part 10.stl, 3D - Part 11.stl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]
2026-01-13 Various printing trials, mostly 3D.
    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
    [2cable_chain.stl, 3D - Part 10.stl, 3D - Part 11.stl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]
2026-01-14 More stls. Created somthing of a plan for control.
    See control_plan.md
    Next steps: Figure out how to control motors and interface with ROS.
    [3D - Part 10.stl, 3D - Part 11.stl, 3D - Part 12.stl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]
2026-01-14 Formalizing more of control plan.
    Setting details on motor specifics and concept of control with glove.
2026-01-14 More parts
    [3D - Part 17.stl, 3D - Part 18.stl, 3D - Part 19.stl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]
2026-01-27 New tentacle, spool, base designs
    [base_v3.stl, base_with_slots.stl, flex_slider.stl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]
2026-01-28 New testing spools
    [spool_v4.stl, spool_v5.stl]
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2026-01-29 Created a node that can use all Dynamixel controls
    single_motor_test has a subscriber that will set the control mode of the
    motor.
    There's also a subscriber on the /set_position topic that will set the
    goal. There's only that one topic, it doesn't matter what the control
    mode is.
    Next steps: Read sensors
2026-01-29 Created messaage and service for setting motors.
    Goal.msg sets the goal of motor "goal.id" to goal.goal. What this goal
    represents (position, velocity, etc) is not set by the message.
    Set_Mode.srv is to be used to set the control mode of the motors. The
    response represents if the mode was succesfully changed
2026-01-29 Transitioning away from dynamixel_sdk packages
    Switched over to polydact_interfaces Goal message and Mode server in
    single_motor_test.
    single_motor_test:
    + Added switch_mode_cb to use new Goal service.
    ++ created several functions to support this change.
    Next steps: Continue transition
2026-01-29 Created goal callback (did not add PWM) Also autoformatted
    Next steps: add PWM
2026-01-29 Removed old dynamixel_sdk_example code
    Next steps: Add a torque detection cutoff. Coordinate three motors.
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2026-01-31 Added new glove parts.
    [flex_slider_v3.stl, flex_slider_v4.stl, hand_bracket_v1.stl]
2026-02-02 Can control a motor with a gloved flex sensor
    Next steps: Write launch file, control 3 motors.
2026-02-02 Created launch file for single motor
    [single_motor.launch.xml]
2026-02-02 three motor setup works with glove
    [motors.launch.xml]
2026-02-02 Added mode 0 to turn off motors in mode service
    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
    [motors.launch.xml]
2026-02-03 Elaborated on motor_id parameter in launchfile.
    Next steps: Creating sensor class in the serial reader node.
    [motors.launch.xml]
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2026-02-03 Too many changes, all untested
    polydact_interfaces/msg/Goal is now MotorState
    motos.launch.xml:
    + Added all Parameters
    motor_coordinator:
    > Moved getting and publishing state code from timer to own functions
    > All motor pos, vel, loads are now published
    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
    [motors.launch.xml]
2026-02-04 Changed the state messages to an array, but this appears to have slowed it way down
    [motors.launch.xml]
2026-02-04 Further array fixing
    [motors.launch.xml]
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2026-02-04 Fixed lag issue by adding separate reader timer.
    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
2026-02-04 Added better error handling
    [motor_coordinator.py]
2026-02-04 Added plotjuggler config arg, fixed MotorState subscriber
    [motors.launch.xml]
2026-02-04 Changed logging, fixed MotorState cb issue
    [motor_coordinator.py]
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2026-02-05 Removed last vestiges of other control modes.
    [motors.launch.xml]
2026-02-06 Added mold stls, updated purchases
    [mold_bottom.stl, mold_top.stl]
2026-02-11 new designs
    [baseV6.stl, frameV6.stl, mold_bottom_v2.stl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]
2026-02-16 Serial logger prints port, shorter calibration
    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
2026-02-16 Works
    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
    [motors.launch.xml]
2026-02-18 New models, new IDs
    [3D for full printing - 3D Tentacle (1).stl, 3D for full printing - 3D Tentacle (10).stl, 3D for full printing - 3D Tentacle (11).stl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]
2026-02-22 Updating typos and design directories
    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
    [2cable_chain.stl, 3D - Part 1.stl, 3D - Part 10.stl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]
2026-02-22 Updating stl files
    [motor frame.stl, motor_frame.stl, spool_body.stl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]
2026-02-22 Removed or commented use of MotorGoalArray
    [motors.launch.xml]
2026-02-22 Adding calibration and mapping to sensor and readr
    Next steps: Finish fixing up the publishing timer in serial_reader.
    [sensor.py]
2026-02-22 Updated hand bracket for fit with PLA bones
    [hand_bracket.stl]
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2026-02-22 New plotjuggler config, old one kept breaking
    [motors.launch.xml]
2026-02-22 Fixed line too long in motor_coordinator.py
    [motor_coordinator.py]
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2026-02-22 New flex slider. Should be easier to sew
    [flex_slider.stl]
2026-02-24 Changed plotjuggler config, made plogjuggler exit
    [motors.launch.xml]
2026-02-24 Attempting to read motor pos, vel, eff
    Next steps: Need to fix how I'm reading efforts
    [dynamixel_interface.py, motor_coordinator.py]
2026-02-24 Changing stl folder name, creating circuit folder
    [3D for full printing - Part 10.stl, 3D for full printing - Part 11.stl, 3D for full printing - Part 12.stl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]
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2026-03-08 new STLs, adding MotorGoal
    [3D for full printing - Part 10.stl, 3D for full printing - Part 11.stl, 3D for full printing - Part 12.stl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]
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2026-03-08 venv removal
    [pyvenv.cfg]
2026-03-08 Name changes, starting full Pi ADC sensor node
    [motors.launch.xml]
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2026-03-08 Changes for allowing sensor-motor remapping.
    motors.launch.xml:
    + Added arg sensor_ids so that sensors and motors can have different ids.
    dynamixel_interface.py:
    ~ Changed Motor initialization to set mode to off at startup.
    + Created set_off function so that motors can be turned off from the
    ++ main node using motor.set_off instead of using
    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
    [motors.launch.xml]
2026-03-08 Finished main flow of sensor remapping.
    sensor.py:
    ~ Changed name of set_average to fill_averate
    serial_reader.py:
    + Created freeze() to set motor velocities to 0 and kill the timer
    ++ freeze(False) will restart the timer with sensor values reset to 0
    + Added checking at the end of sensor remapping.
    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
    [sensor.py, serial_sensor_node.py]
2026-03-08 Finished sensor remapping. Untested.
    + Added selector.min and selector.max for figuring out which sensor is
    ++ being flexed during remapping.
    ~ freeze(freeze_on, read): Added argument for pausing read timer as
    ~~ well as the publishing timer.
    + get_max_diff(reads): Returns the id of the sensor which was flexed
    the most over the selected number of serial reads.
    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
    [sensor.py, serial_sensor_node.py]
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2026-03-08 Added plotter.launch.xml Fixed plotjuggler config Fixed other launch file formatting Changed sensor smoothing to 1 since ADC read is much faster and smoother
    [sensor.py]
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2026-03-10 Fixing ADC noise (Also sewing issue)
    [pi_adc_sensor_node.py, sensor.py]
2026-03-16 New motor frame with wire slot
    [motor_frame.stl]
2026-03-16 Modified motor frame
    [motor_frame.stl]
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2026-04-01 Reorganize /design
    [adjustable_mount - hand_bracket.stl, adjustable_mount_hand_bracket.stl, adjustable_mount_socket.stl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]
